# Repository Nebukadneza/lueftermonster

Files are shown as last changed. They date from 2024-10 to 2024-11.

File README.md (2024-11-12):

# Lüftermonster

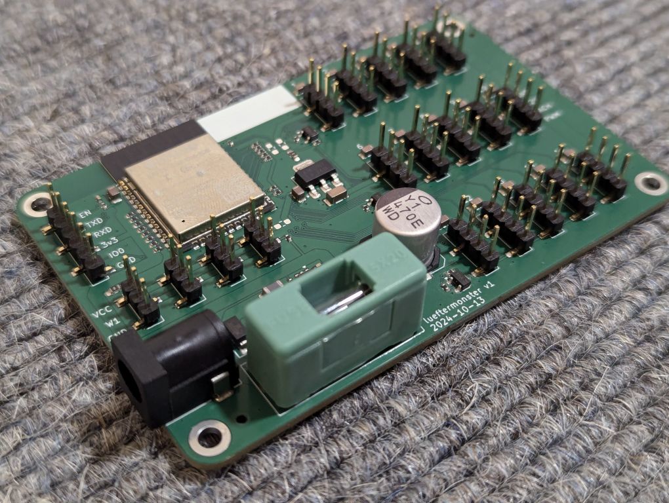
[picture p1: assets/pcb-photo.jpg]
Photo of the Lüftermonster PCB The Lüftermonster PCB


## TL;DR:
You want to control up to 15 PC Fans by PWM, read the RPM of every single one, attach up to 4 DS18b20 Temperature Probes, and have all this exposed by API, Web-interface or into Home-Assistant? This is for you!

## Description
Many water based central heating systems that use radiators benefit from a reduced system temperature. Whether it´s fuel-value gas or oil, or a heat-pump, reducing the systems primary temperature results in energy savings.

Radiators can only radiate a certain amount of heat defined by their construction and size - unless we force some air through them! This can be done passively by building a "chimney" around them and using the chimney-effect, and/or by attaching fans. Many commercially available fan-retrofitting kits or even radiators with fans included use noisy low quality fans, don´t allow for a lot of control, and are often very expensive. So you might want to add your own.

Lüftermonster is a project that provides you with a hardware PCB and software to control up to 15 PC Fans, allowing you to make them noiseless by PWM. The tacho signals (RPM) of all fans are monitored so you can monitor them and detect broken fans. Furthermore, you can add up to 4 DS18b20 temperature sensors in order to measure water- and air-temperature to finely control your fan-speed depending on your heating and room situation. Lüftermonster is WIFI-enabled by relying on a trusty ESP32.

By implementing Lüftermonster using [ESPHome](https://esphome.io/), we make it maintainable and easily customizable. It integrates seamlessly into [Home-Assistant](https://www.home-assistant.io/) and other home-automation solutions. If you don´t have or want one, you can use the local API or web-based interface to control and monitor your Lüftermonster.

The hardware is designed so that it can be easily and affordably ordered off [JLCPCB](https://jlcpcb.com/) ready-made with components soldered by them!

# Building one
## What you need
- Lüftermonster PCB(s).
- A USB-to-Serial adapter, like the ubiquitous "FTDI" ones. Find them off your local maker store, EBay, AliExpress, Amazon or similar.
- "Dupont" female-to-female cables to connect Lüftermonster to the USB-to-Serial adapter.
- 20x5mm 2A slow fuses.
- Up to 15 PC Fans per Lüftermonster: 12V, 4-pin.
- (Optional: up to 4 DS18b20 temperature probes per Lüftermonster, including 3-pin cables)

## Hardware
### Fabrication
Gerber files and BOM/CPL data compatible with the JLCPCB assembly service can be found in the `fab` directory. This is a 2-layer PCB compatible with their "Economic" class PCBA service.

### Stuffing options

A few stuffing options are available on the PCB. The corresponding 0R resistors use 0603 sizes (compared to the 0402 size used for everything else) to be more convenient to rework with basic equipment. If you don't have KiCad installed, you can use the [Interactive HTML BOM](fab/ibom.html) to locate the components on the board.

* PWM output voltage levels. Exactly one of the following 0R resistors must be populated.
  * R10: 5V (default)
  * R11: 3.3V
  * R13: Equal to supply voltage (i.e. usually 12V)
* 1-wire supply: Exactly one of the following 0R resistors must be populated.
  * R32: 3.3V (default)
  * R12: 5V

## Software
### Preparation
Install ESPHome, please refer to their excellent ["Getting Started" Sections](https://esphome.io/). Note: You only need to get esphome itself running, not write any YAML-Files yourself.

Copy `firmware/secrets.yaml.template` to `firmware/secrets.yaml`, and edit according to your environment.

Open and edit `firmware/lueftermonster.yaml` according to your environment. Note: If you have multiple Lüftermonsters, please assign unique and meaningful names like "lueftermonster-livingroom-left" or similar.

### Programming
Connect the USB-to-Serial adapter to your Lüftermonster, as follows:
  - VCC -> 3v3
  - GND -> GND
  - RX -> TX
  - TX -> RX
  - EN -> CTS
  - IO0 -> DTR

Attach your USB-to-Serial adapter to your computer

Follow the ESPHome Getting-Started guide you´ve chosen to "run" or "upload" `firmware/lueftermonster.yaml`.

Note: `esptool`, which is internally used by ESPHome to program the ESP32 tries to reset the ESP32 and bring it into programming mode. If this does not work, it may be that "Automatic bootloader mode" does not work. Please [refer to the documentation](https://docs.espressif.com/projects/esptool/en/latest/esp32/advanced-topics/boot-mode-selection.html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).

### Usage
After a brief period, you should be able to open `http://<the-name-you-set-in-the-yaml>.local/`, for example http://lueftermonster-livingroom-left.local/ .

Now, you can control the fan speed, and check the fans current RPMs. Note: RPM are not updated often, so it make take a while for all of them to display, and for speed changes to become visible. This is intentional since the information is most useful for outage detection, and does not need to be reported often.

To connect to Home-Assistant refer to the [ESPHome documentation](https://esphome.io/guides/getting_started_hassio#connecting-your-device-to-home-assistant)

### Connect a fan
Since the "proper" PC Fan connectors are not cheaply sourcable from JLCPCB (and THT parts incur a hand-soldering fee/delay), we cheaped out by using standard 2.54mm connection pins. This works, but

_**IS NOT SAFE TO CONNECT IN REVERSE!**_

So you need to pay attention to how you connect your fans. Refer to the silk-screen on the right of Lüftermonster for the pinout of the connectors. With the two "latches" of a standard PC Fan connector, it is correct to connect the fan like this:
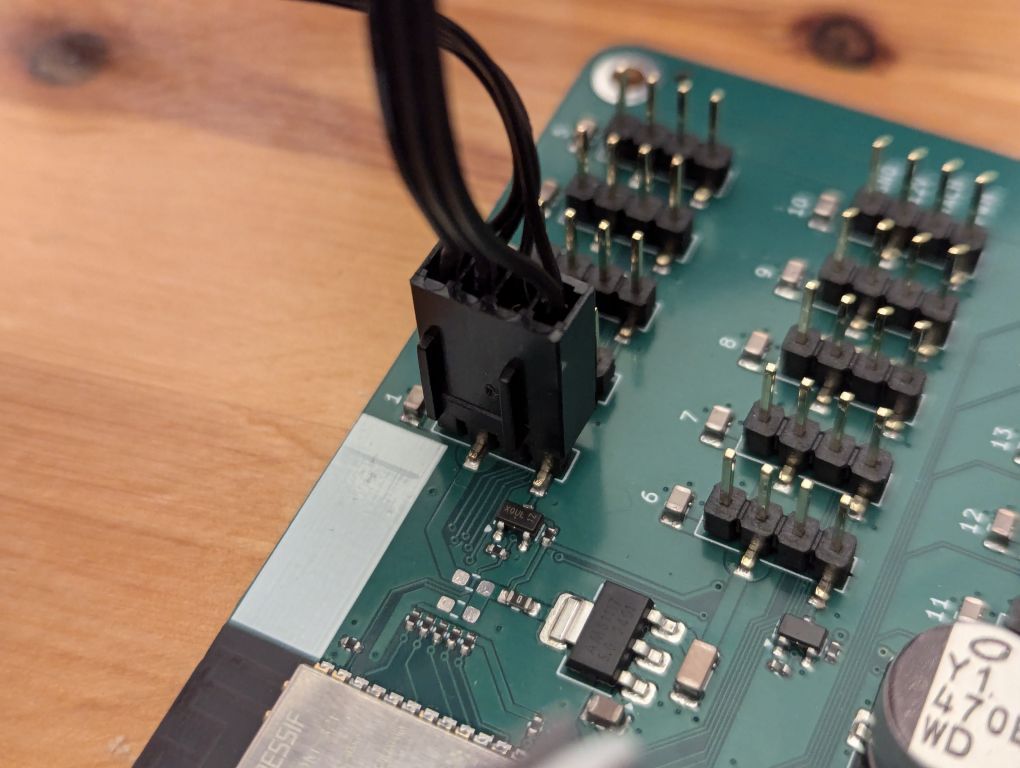
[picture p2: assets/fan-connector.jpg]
Close-up of a PC Fan connector on the PCB CORRECT polarity Connection


### Connecting DS18b20 Temperature Sensors
TODO: Section about DS18b20 address finding and such.

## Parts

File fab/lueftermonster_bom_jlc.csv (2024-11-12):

Designator | Footprint | SPN
C4,C9 | C_0402_1005Metric | C15195
C1,C3 | C_0805_2012Metric | C28233
C11,C12,C13,C14,C15,C16,C17,C18,C19,C20,C21,C22,C23,C24,C25 | C_0805_2012Metric | C215803
C6,C7 | C_1206_3216Metric | C29823
C2,C8,C10 | C_0805_2012Metric | C440198
C5 | CP_Elec_10x10 | C251022
D1 | D_SMA | C110042
D2 | D_SOD-123F | C8598
F1 | XFCN_PTF-77 | C717030
FB1,FB2 | L_1206_3216Metric | C337884
J1 | XUNPU_DC-005-A200 | C720557
J2,J3,J4,J5,J6,J7,J8,J9,J10,J11,J12,J13,J14,J15,J16 | PinHeader_1x04_P2.54mm_Vertical_SMD_Pin1Right | C780062
J17 | PinHeader_1x06_P2.54mm_Vertical_SMD_Pin1Left | C2883763
J18,J19,J20,J21 | PinHeader_1x03_P2.54mm_Vertical_SMD_Pin1Left | C2883760
L1 | L_1008_2520Metric | C576403
Q2,Q3,Q4 | SOT-23 | C20917
Q1 | Diodes_PowerDI3333-8 | C461090
R10,R32 | R_0603_1608Metric_Pad0.98x0.95mm_HandSolder | C21189
R6,R7,R8 | R_0402_1005Metric | C102864
R9 | R_0402_1005Metric | C25900
R1,R2,R5,R14,R15,R16,R17,R18,R19,R20,R21,R22,R23,R24,R25,R26,R27,R28,R29,R30,R31,R33 | R_0402_1005Metric | C25744
R4 | R_0402_1005Metric | C26956
R3 | R_0402_1005Metric | C25897
U3 | SOT-223-3_TabPin2 | C6187
U2 | SOT-23-6 | C41240
U1 | ESP32-WROOM-32D | C701342

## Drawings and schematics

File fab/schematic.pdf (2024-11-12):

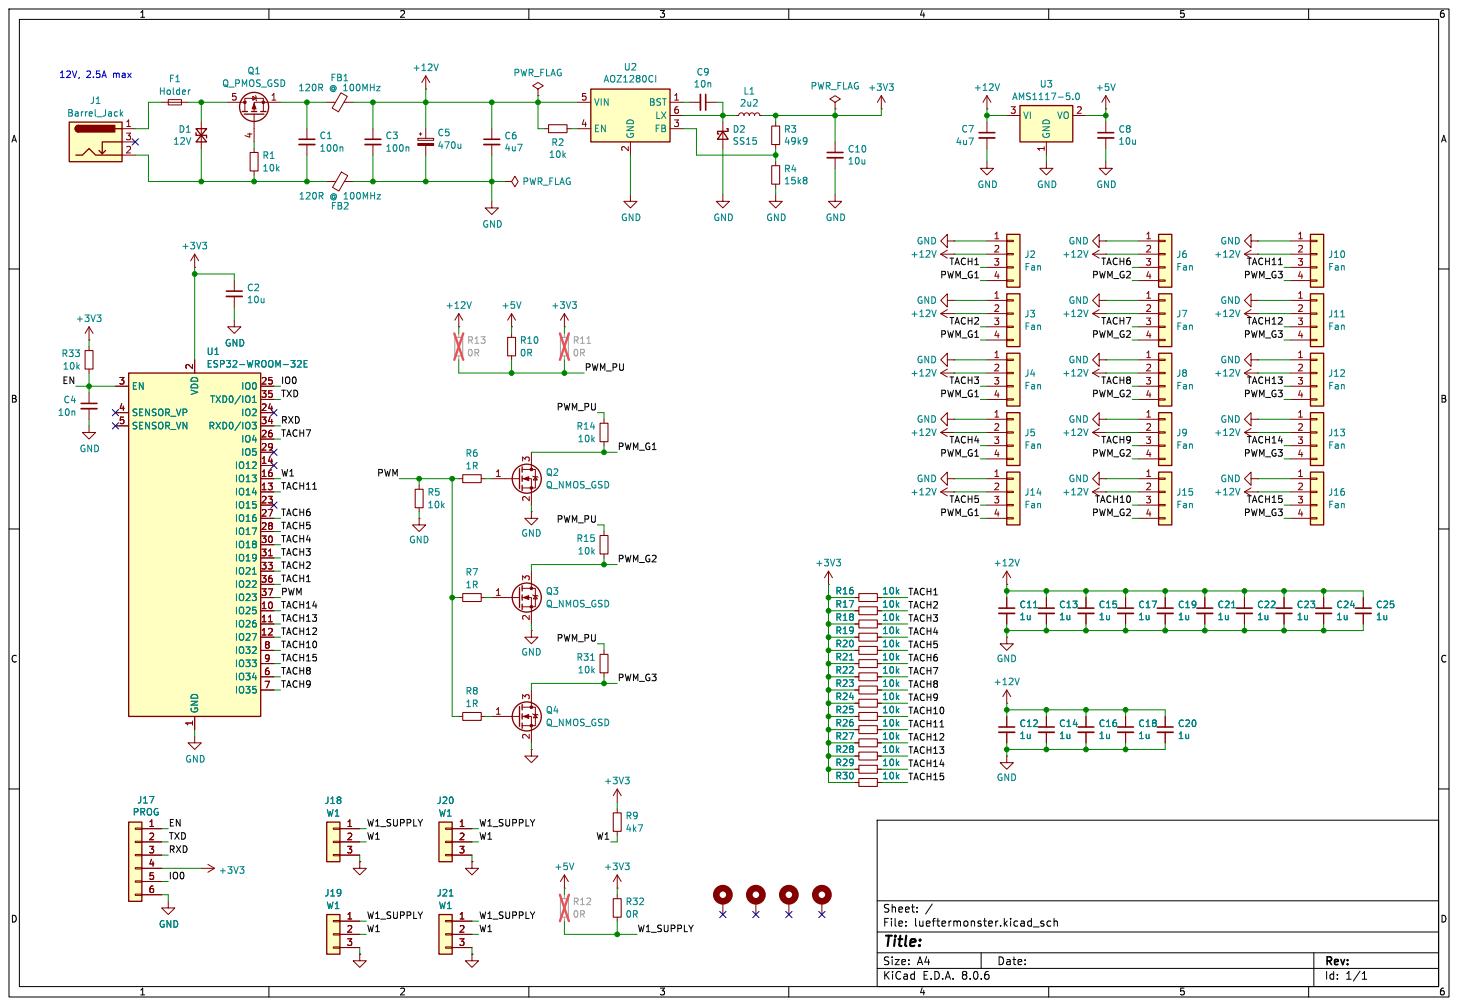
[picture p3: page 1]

1 VO 2 VI 3 U3 AMS1117-5.0 +12V GND GND

Id: 1/1 Title: File: lueftermonster.kicad_sch Sheet: /

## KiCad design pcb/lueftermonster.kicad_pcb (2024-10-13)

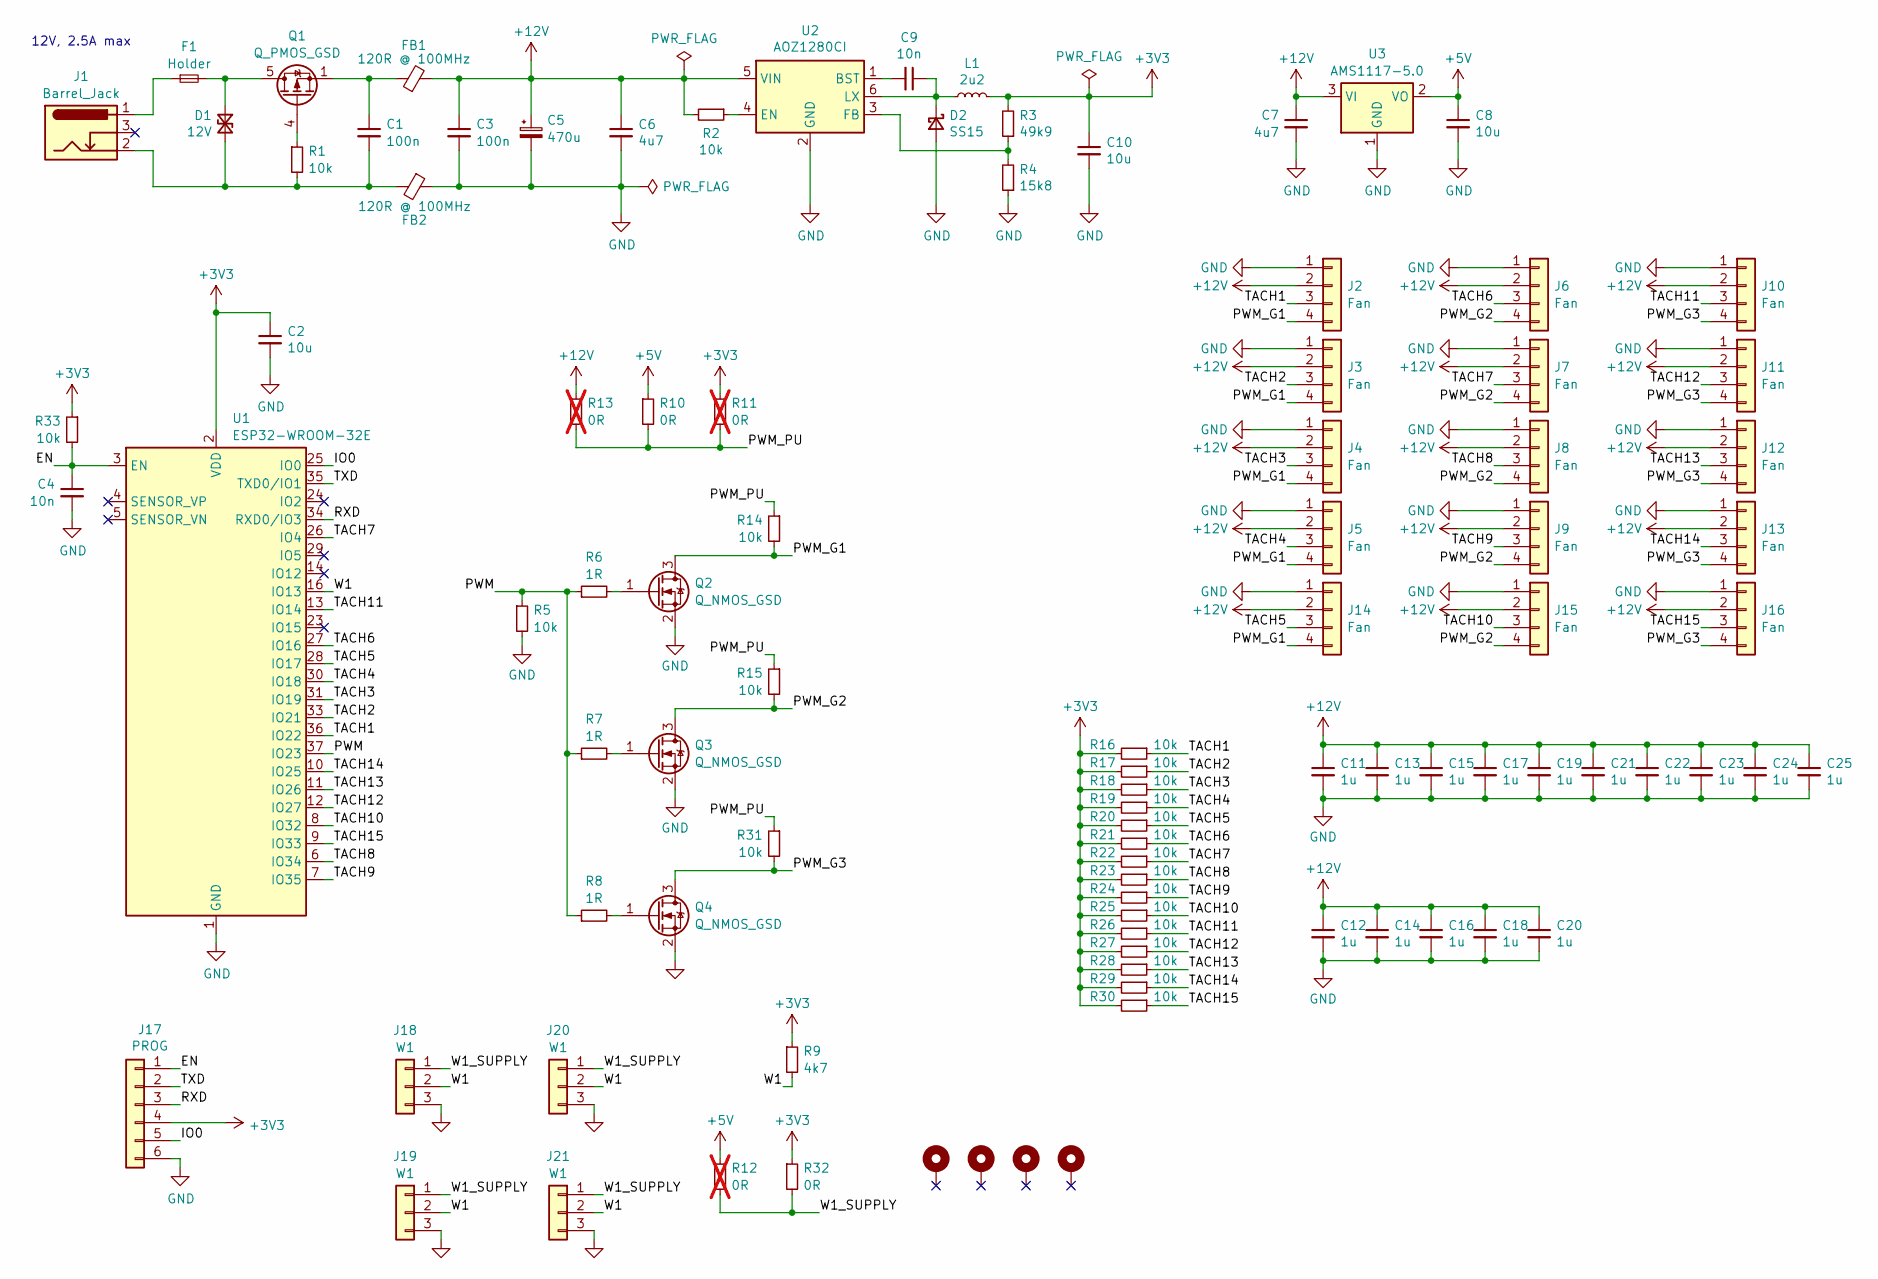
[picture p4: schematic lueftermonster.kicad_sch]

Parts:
C1, C3: 100n; C_0805_2012Metric; MPN CL21B104KCFNNNE; LCSC C28233
C2, C8, C10: 10u; C_0805_2012Metric; MPN GRM21BR61H106KE43L; Digikey 399-8012-1-ND
C4, C9: 10n; C_0402_1005Metric; MPN CL05B103KB5NNNC; LCSC C15195
C5: 470u; CP_Elec_10x10; MPN UWD1E471MCL1GS; LCSC C251022
C6, C7: 4u7; C_1206_3216Metric; MPN 1206B475K500NT; LCSC C29823
C11, C12, C13, C14, C15, C16, C17, C18, C19, C20, C21, C22, C23, C24, C25: 1u; C_0805_2012Metric; MPN 0805B105K500NT; LCSC C215803
D1: 12V; D_SMA; MPN SMAJ12CA; LCSC C110042
D2: SS15; D_SOD-123F; MPN B5819W SL; LCSC C8598
F1: Holder; XFCN_PTF-77; MPN PTF-77; LCSC C717030
FB1, FB2: 120R @ 100MHz; L_1206_3216Metric; MPN BLM31KN121SN1L; LCSC C337884
H1, H2, H3, H4: MountingHole_Pad; MountingHole_3.2mm_M3_ISO14580_Pad
J1: Barrel_Jack; XUNPU_DC-005-A200; MPN DC-005-A200; LCSC C720557
J2, J3, J4, J5, J6, J7, J8, J9, J10, J11, J12, J13, J14, J15, J16: Fan; PinHeader_1x04_P2.54mm_Vertical_SMD_Pin1Right; MPN X6511WVS-04H-C60D48R1; LCSC C780062
J17: PROG; PinHeader_1x06_P2.54mm_Vertical_SMD_Pin1Left; MPN X6511WVS-06H-C60D48R2; LCSC C2883763
J18, J19, J20, J21: W1; PinHeader_1x03_P2.54mm_Vertical_SMD_Pin1Left; MPN X6511WVS-03H-C60D48R2; LCSC C2883760
L1: 2u2; L_1008_2520Metric; MPN DFE252012F-2R2M=P2; LCSC C576403
Q1: Q_PMOS_GSD; Diodes_PowerDI3333-8; MPN DMP4025SFG-13; LCSC C461090
Q2, Q3, Q4: Q_NMOS_GSD; SOT-23; MPN AO3400A; LCSC C20917
R1, R2, R5, R14, R15, R16, R17, R18, R19, R20, R21, R22, R23, R24, R25, R26, R27, R28, R29, R30, R31, R33: 10k; R_0402_1005Metric; MPN 0402WGF1002TCE; LCSC C25744
R3: 49k9; R_0402_1005Metric; MPN 0402WGF4992TCE; LCSC C25897
R4: 15k8; R_0402_1005Metric; MPN 0402WGF1582TCE; LCSC C26956
R6, R7, R8: 1R; R_0402_1005Metric; MPN RTT021R00FTH; LCSC C102864
R9: 4k7; R_0402_1005Metric; MPN 0402WGF4701TCE; LCSC C25900
R10, R32: 0R; R_0603_1608Metric_Pad0.98x0.95mm_HandSolder; MPN 0603WAF0000T5E; LCSC C21189
R11, R12, R13: 0R; R_0603_1608Metric_Pad0.98x0.95mm_HandSolder; MPN 0603WAF0000T5E; LCSC C21189; not fitted
U1: ESP32-WROOM-32E; ESP32-WROOM-32D; LCSC C701342
U2: AOZ1280CI; SOT-23-6; MPN AOZ1280CI; Digikey 785-1277-1-ND
U3: AMS1117-5.0; SOT-223-3_TabPin2; MPN AMS1117-5.0; LCSC C6187

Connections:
+3V3: C2.1, C10.1, J17.4, L1.2, R3.2, R9.1, R11.1, R16.2, R17.2, R18.2, R19.2, R20.2, R21.2, R22.2, R23.2, R24.2, R25.2, R26.2, R27.2, R28.2, R29.2, R30.2, R32.1, R33.1, U1.2 (VDD)
+5V: C8.1, R10.1, R12.1, U3.2 (VO)
+12V: C3.1, C5.1, C6.1, C7.1, C11.1, C12.1, C13.1, C14.1, C15.1, C16.1, C17.1, C18.1, C19.1, C20.1, C21.1, C22.1, C23.1, C24.1, C25.1, FB1.2, J2.2, J3.2, J4.2, J5.2, J6.2, J7.2, J8.2, J9.2, J10.2, J11.2, J12.2, J13.2, J14.2, J15.2, J16.2, R2.2, R13.1, U2.5 (VIN), U3.3 (VI)
/EN: C4.1, J17.1, R33.2, U1.3 (EN)
/IO0: J17.5, U1.25 (IO0)
/PWM: R5.1, R6.1, R7.1, R8.1, U1.37 (IO23)
/PWM_G1: J2.4, J3.4, J4.4, J5.4, J14.4, Q2.3 (D), R14.2
/PWM_G2: J6.4, J7.4, J8.4, J9.4, J15.4, Q3.3 (D), R15.2
/PWM_G3: J10.4, J11.4, J12.4, J13.4, J16.4, Q4.3 (D), R31.2
/PWM_PU: R10.2, R11.2, R13.2, R14.1, R15.1, R31.1
/RXD: J17.3, U1.34 (RXD0/IO3)
/TACH1: J2.3, R16.1, U1.36 (IO22)
/TACH2: J3.3, R17.1, U1.33 (IO21)
/TACH3: J4.3, R18.1, U1.31 (IO19)
/TACH4: J5.3, R19.1, U1.30 (IO18)
/TACH5: J14.3, R20.1, U1.28 (IO17)
/TACH6: J6.3, R21.1, U1.27 (IO16)
/TACH7: J7.3, R22.1, U1.26 (IO4)
/TACH8: J8.3, R23.1, U1.6 (IO34)
/TACH9: J9.3, R24.1, U1.7 (IO35)
/TACH10: J15.3, R25.1, U1.8 (IO32)
/TACH11: J10.3, R26.1, U1.13 (IO14)
/TACH12: J11.3, R27.1, U1.12 (IO27)
/TACH13: J12.3, R28.1, U1.11 (IO26)
/TACH14: J13.3, R29.1, U1.10 (IO25)
/TACH15: J16.3, R30.1, U1.9 (IO33)
/TXD: J17.2, U1.35 (TXD0/IO1)
/W1: J18.2, J19.2, J20.2, J21.2, R9.2, U1.16 (IO13)
/W1_SUPPLY: J18.1, J19.1, J20.1, J21.1, R12.2, R32.2
GND: C2.2, C3.2, C4.2, C5.2, C6.2, C7.2, C8.2, C10.2, C11.2, C12.2, C13.2, C14.2, C15.2, C16.2, C17.2, C18.2, C19.2, C20.2, C21.2, C22.2, C23.2, C24.2, C25.2, D2.2 (A), FB2.1, J2.1, J3.1, J4.1, J5.1, J6.1, J7.1, J8.1, J9.1, J10.1, J11.1, J12.1, J13.1, J14.1, J15.1, J16.1, J17.6, J18.3, J19.3, J20.3, J21.3, Q2.2 (S), Q3.2 (S), Q4.2 (S), R4.1, R5.2, U1.1 (GND), U1.15 (GND), U1.38 (GND), U1.39 (GND), U2.2 (GND), U3.1 (GND)
unnamed: C1.1, FB1.1, Q1.1 (S), Q1.2 (S), Q1.3 (S)
unnamed: D1.1 (A1), F1.2, Q1.5 (D)
unnamed: C1.2, D1.2 (A2), FB2.2, J1.2, R1.2
unnamed: C9.1, D2.1 (K), L1.1, U2.6 (LX)
unnamed: F1.1, J1.1
unnamed: Q1.4 (G), R1.1
unnamed: Q2.1 (G), R6.2
unnamed: Q3.1 (G), R7.2
unnamed: Q4.1 (G), R8.2
unnamed: C9.2, U2.1 (BST)
unnamed: R2.1, U2.4 (EN)
unnamed: R3.1, R4.2, U2.3 (FB)

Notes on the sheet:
12V, 2.5A max

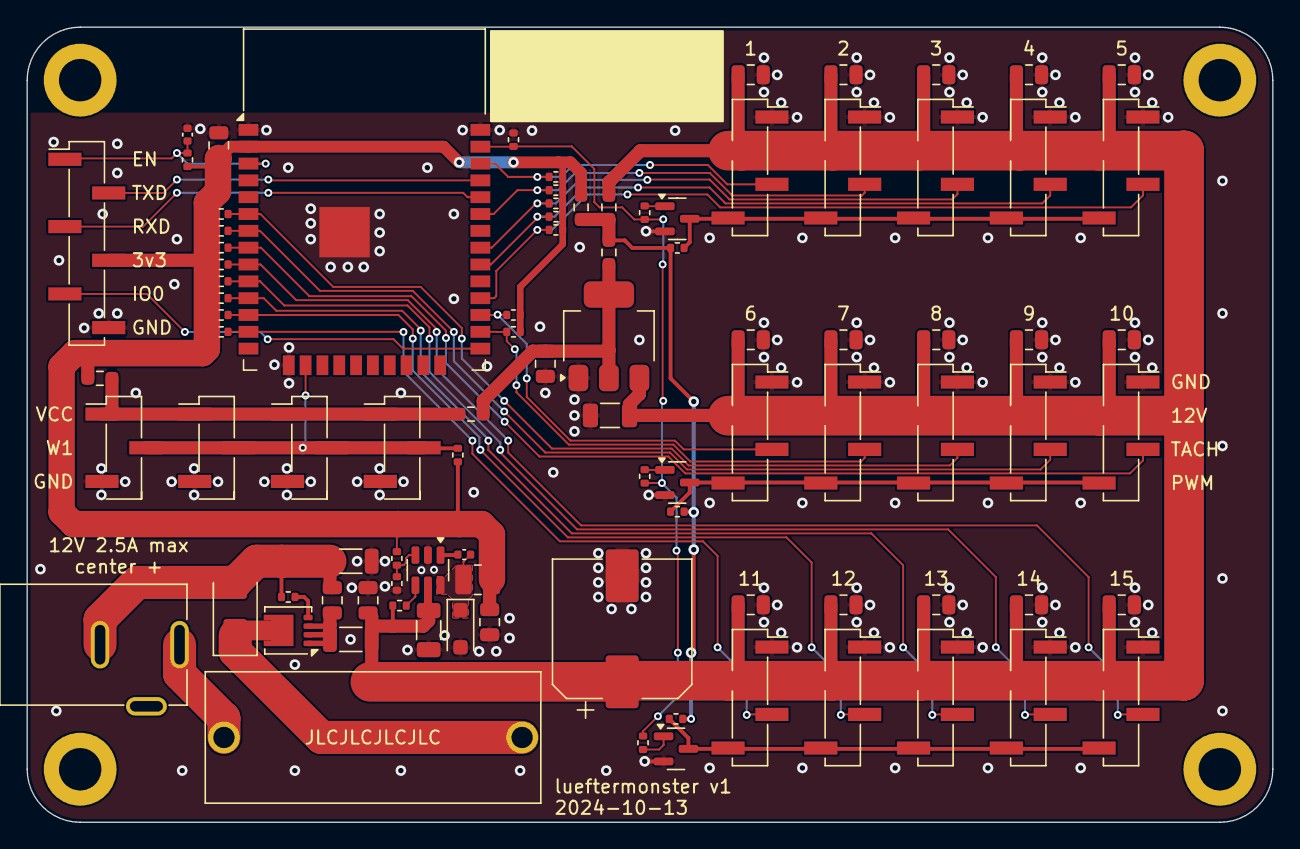
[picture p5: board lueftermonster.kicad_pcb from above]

Board: 2 copper layers, 94.0 x 60.0 mm, 96 parts (0 on the bottom side), 42 nets.

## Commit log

2024-06-05 more bom
    [lueftermonster.kicad_sch]
2024-06-05 unfuck fields even harder
    [lueftermonster.kicad_sch]
2024-06-05 more bom, all the heavy hitters are in now
    [lueftermonster.kicad_sch]
2024-06-05 bullshit placing to make gerbers sane
    [lueftermonster.kicad_pcb]
2024-10-12 use 100mil headers for fans
    [lueftermonster.kicad_pcb, lueftermonster.kicad_sch]
2024-10-12 finalize bom, add LED
    [lueftermonster.kicad_sch]
2024-10-12 0 nets
    [lueftermonster.kicad_pcb]
2024-10-13 DRC clean
    [lueftermonster.kicad_pcb]
2024-10-13 update bom
    [lueftermonster.kicad_sch]
2024-10-13 replace out of stock 1R 0402
    [lueftermonster.kicad_sch]
2024-11-11 Add fan connection section to readme
2024-11-12 add fab data
    [lueftermonster_bom_jlc.csv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]
2024-11-12 Move PCB Design files to subdir
    [lueftermonster.kicad_pcb, lueftermonster.kicad_sch]
